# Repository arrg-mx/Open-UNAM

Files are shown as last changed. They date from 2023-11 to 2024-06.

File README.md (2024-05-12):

# Open-UNAM

## Contenido

- [Objetivo](#objetivo)
- [Desarrollo](#desarrollo)
- [Equipo](#equipo)
- [Referencias](#referencias)

## Objetivo

Diseñar he implementar una plataforma de pruebas basada en los parámetros del robot Open-Manipulator, la cual se realizán pruebas de algoritmos de manipulación de objetos.

## Desarrollo

- [X] Diseñar el modelo virtual de la platadorma del robot con 5 grados de libertad.
- [x] Cálcular el modelo cinemático inverso de las velocidades del robot para la realización de trayectorias.
- [ ] Implementar el modelo en Simulink del control del robot.
- [ ] Realizar pruebas de funcionamiento del sistema realizando una tarea simple.

Metas 2024-2
- [ ] Hacer una revisión de los componentes con los que se cuentan para la construcción del robot.
- [ ] Realizar la manufactura de las piezas del robot y realizar pruebas de ensamble.
- [ ] Rediseñar la base del robot para que el robot sea estable y garantice el correcto funcionamiento de su actuador.
- [ ] Trabajar en una interfaz de control de los motores en Matlab para que el robot realice una tarea específica. 

## Equipo

**Integrantes del proyecto:**

| Nombre | Observaciones | Semestre |
| :---| :--- | :--- |
| M.I. Erik Peña Medina | **Responsable** | ---- |
| Díaz Alcalá Leslie Zahori | **Participante** | 2024-1 |
| Chavez López Ana Rosa | **Participante** | 2024-1 |
| Rosas Torres Brian Ulises | **Participante** | 2024-1 |
| Pazarán García Jared | **Participante** | 2024-1 |
| Muñoz Ng Gustavo  | **Participante** | 2024-1 |
| Laureano Uribe Diego  | **Participante** | 2024-1 |
| Colima Flores Mauricio Gibran  | **Participante** | 2024-2 |
| Pascual Hernández Daniel Alfonso | **Participante** | 2024-2 |
| Vilchis Torres Itzel | **Participante** | 2024-2 |
| Rivera Moreno Javier | **Participante** | 2024-2 |

## Referencias

### ¿Dónde empezar?

**Academics**

1. Documentacion motor AX-18 [emanual] (https://emanual.robotis.com/docs/en/dxl/ax/ax-18a/)
2. Documentacion DYNAMIXEL Shield [emanual] (https://emanual.robotis.com/docs/en/parts/interface/dynamixel_shield/)
3. Documentacion OpenManipulator [emanual] (https://emanual.robotis.com/docs/en/platform/openmanipulator_x/overview/)
4. Repositorio ROS [github](https://github.com/ROBOTIS-GIT/open_manipulator/tree/master)
5. Archivos de referencia (Carpeta de CAD) [onshape] (http://www.robotis.com/service/download.php?no=690)

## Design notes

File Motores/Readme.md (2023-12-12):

# Conexión del motor AX-18A Dynamixel con Mathlab

## Conexión del programa con el Dynamixel Wizard:

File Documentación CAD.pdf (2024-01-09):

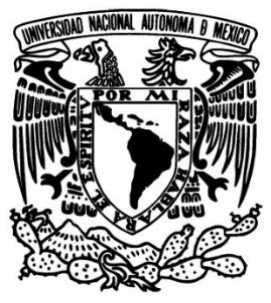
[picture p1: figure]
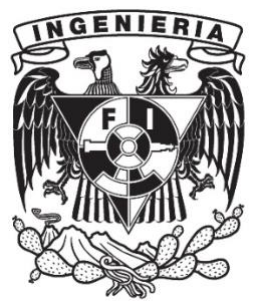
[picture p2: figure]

# Universidad Nacional Autónoma de México Facultad de Ingeniería División de Ingeniería Mecánica e Industrial

# Robótica

## Proyecto Open-Puma

# Documentación CAD

### Alumnos:

### Chávez López Ana Rosa

### Muñoz Ng Gustavo

### Grupo 01

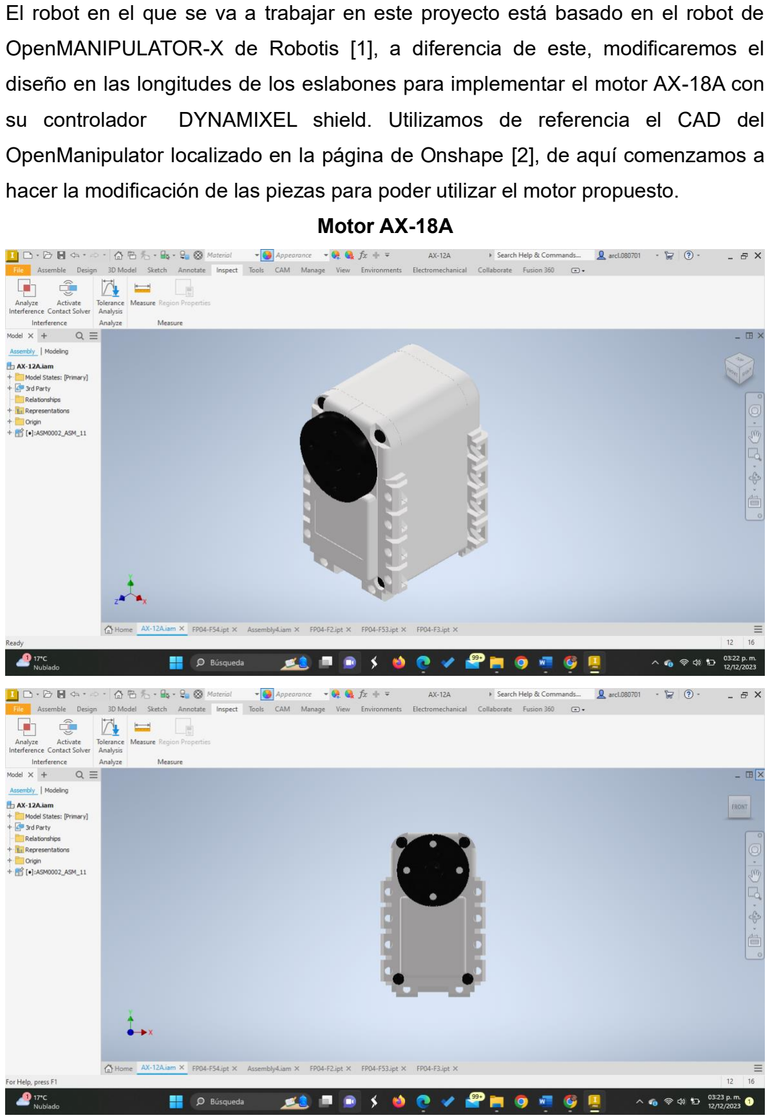
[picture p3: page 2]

El robot en el que se va a trabajar en este proyecto está basado en el robot de

OpenMANIPULATOR-X de Robotis [1], a diferencia de este, modificaremos el

diseño en las longitudes de los eslabones para implementar el motor AX-18A con

su controlador DYNAMIXEL shield. Utilizamos de referencia el CAD del

OpenManipulator localizado en la página de Onshape [2], de aquí comenzamos a

hacer la modificación de las piezas para poder utilizar el motor propuesto.

| Motor AX-18A

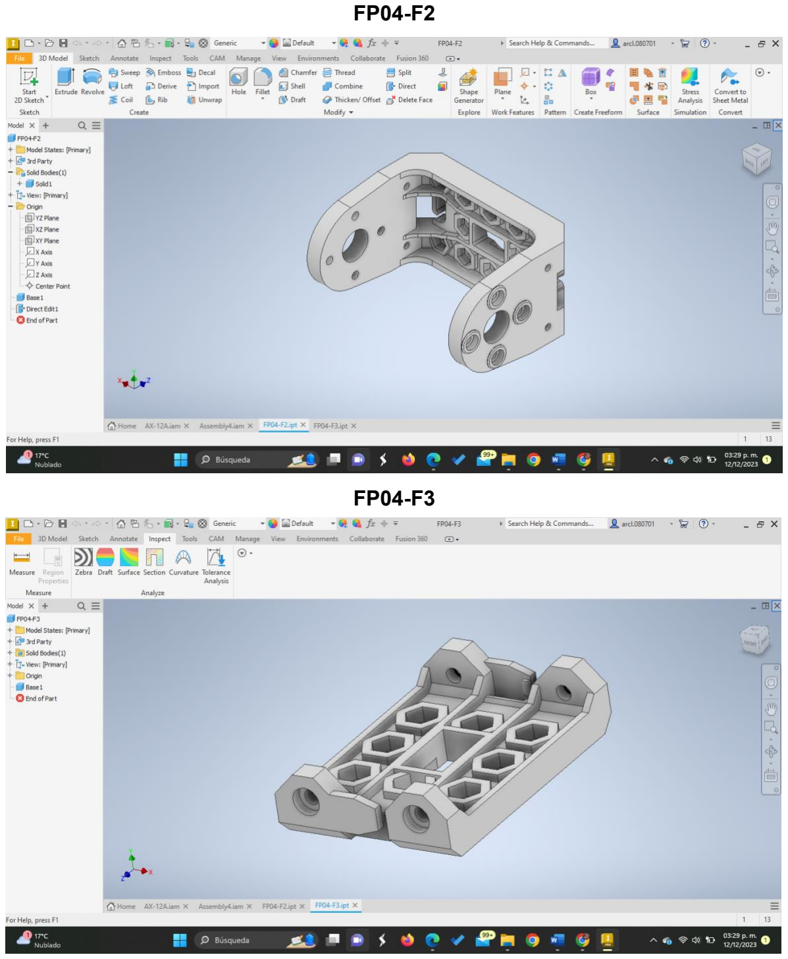
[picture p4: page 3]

FP04-F2

FP04-F3

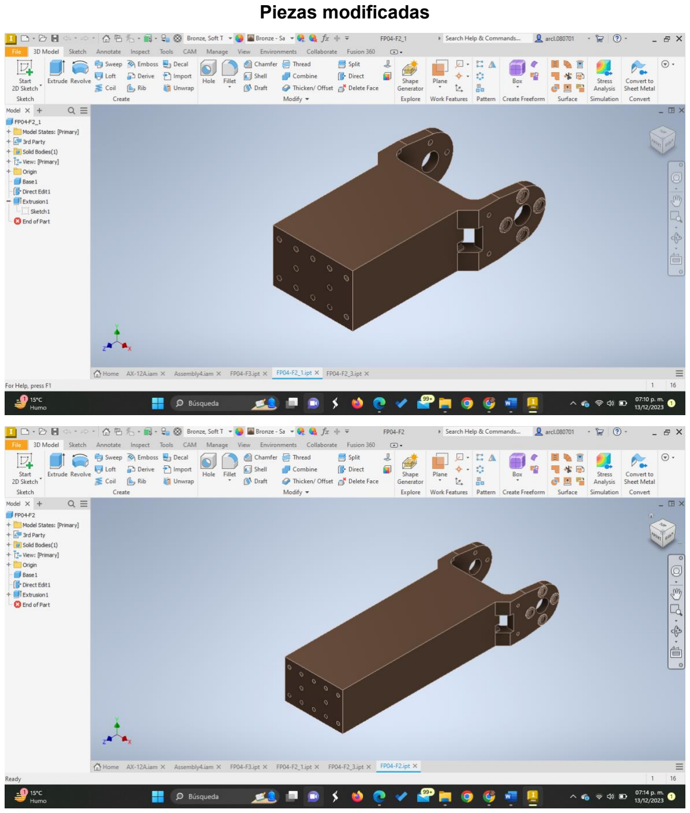
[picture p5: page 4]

Piezas modificadas

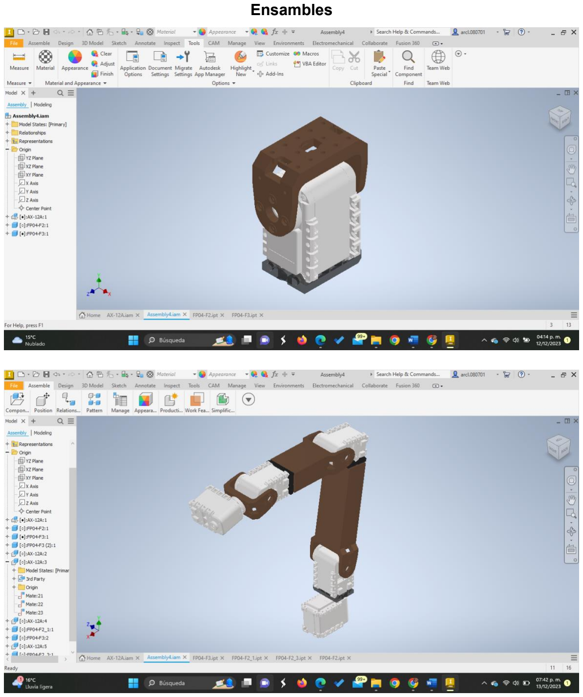
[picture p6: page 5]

Ensambles

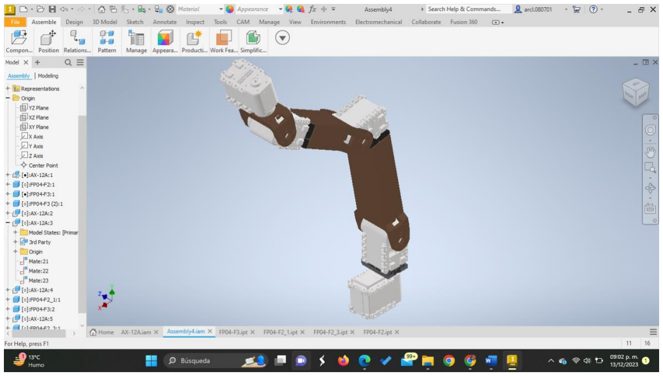
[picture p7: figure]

Referencias

[1] | «Robotis | e-manual,» | 2017. | [En | línea]. | Available:

https://emanual.robotis.com/docs/en/platform/openmanipulator_x/overview/.

[2] | «onshape,» | 2017. | [En | línea]. | Available:

https://cad.onshape.com/documents/9442f03bd8ccac084fda9dd3/w/039e8dbd53e078254

0ea5b0d/e/6f08aa8ac3d3e5b3054f7782. (https://cad.onshape.com/documents/9442f03bd8ccac084fda9dd3/w/039e8dbd53e0782540ea5b0d/e/6f08aa8ac3d3e5b3054f7782)

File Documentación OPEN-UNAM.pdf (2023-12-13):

### Universidad Nacional Autónoma De México

### Facultad de ingeniería

### División de Ingeniería Mecánica e Industrial

### Robótica

### Proyecto: OPEN-UNAM

Chávez López Ana Rosa

Díaz Alcalá Leslie Zahori

Laureano Uribe Diego

Muñoz Ng Gustavo

Pazarán García Jared

Rosas Torres Brian Ulises

### Semestre: 2024-1

El robot en el que se va a trabajar en este proyecto está basado en el robot de OpenMANIPULATOR-X [1], a diferencia de este, modificaremos el diseño en las longitudes de los eslabones para implementar el motor AX-18A con su controlador DYNAMIXEL shield.

Utilizamos de referencia el CAD del OpenManipulator localizado en la página de Onshape [2], de aquí comenzamos a hacer la modificación de los eslabones para poder utilizar el motor propuesto, las especificaciones del motor son las siguientes:

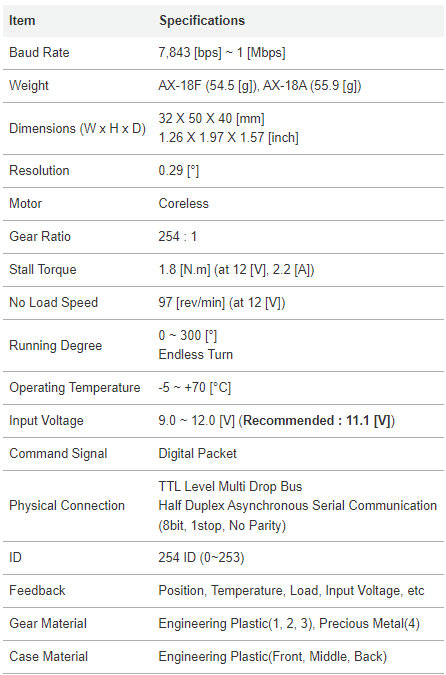
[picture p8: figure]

Este motor cuenta con un área EEPROM y un área RAM. Tabla de control del área EEPROM:

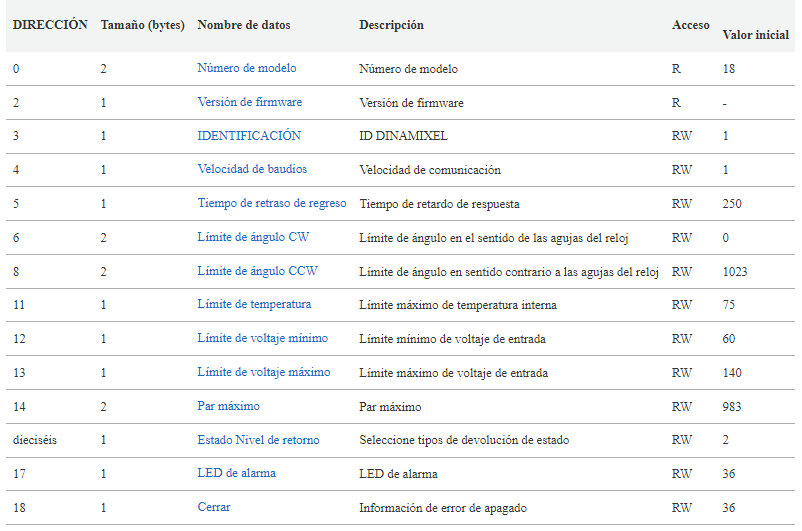
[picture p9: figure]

Área (EEPROM, RAM)
La Mesa de Control se divide en 2 Áreas. Los datos en el área RAM se restablecen a los valores iniciales cuando se restablece la alimentación (volátil). Por otro lado, los datos en el área EEPROM se mantienen incluso cuando el dispositivo está apagado (no volátil).

Tamaño
El tamaño de los datos varía de 1 a 2 bytes dependiendo de su uso. Verifique el tamaño de los datos cuando los actualice con un paquete de instrucciones. Los datos de más de 2 bytes se guardarán según Little Endian .

Acceso
La Mesa de Control tiene dos propiedades de acceso diferentes. La propiedad 'RW' significa permiso de acceso de lectura y escritura, mientras que 'R' significa permiso de acceso de solo lectura. Los datos con la propiedad de solo lectura no se pueden cambiar mediante la instrucción WRITE. La propiedad de solo lectura ('R') se usa generalmente para fines de medición y monitoreo, y la propiedad de lectura y escritura ('RW') se usa para controlar el dispositivo.

Valor inicial
Cada dato en la Tabla de control se restaura a los valores iniciales cuando se enciende el dispositivo. Los valores predeterminados en el área EEPROM son valores iniciales del dispositivo (configuraciones predeterminadas de fábrica). Si un usuario modifica algún valor en el área EEPROM, los valores modificados se restaurarán como valores iniciales cuando se encienda el dispositivo. Los valores iniciales en el área de RAM se restauran cuando se enciende el dispositivo.

Tabla de control del área RAM:

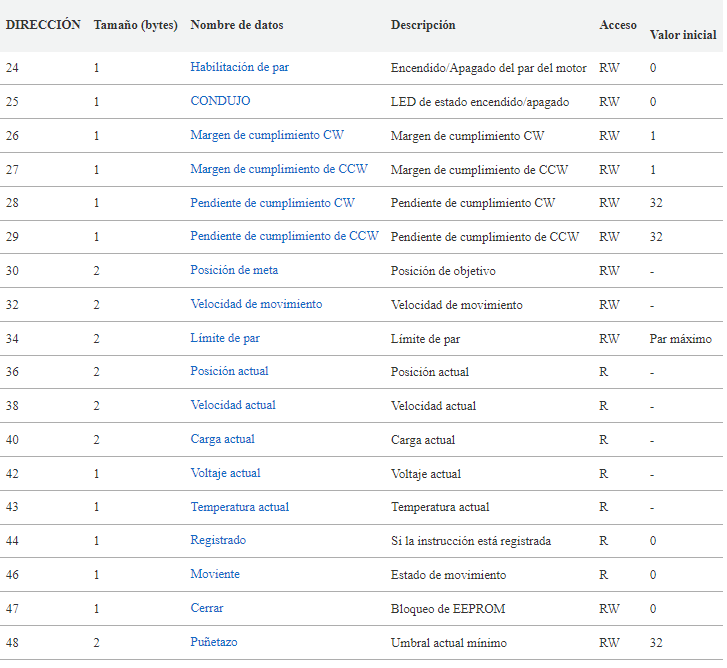
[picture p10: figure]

La velocidad en baudios determina la velocidad de comunicación en serie entre un controlador y DYNAMIXEL.

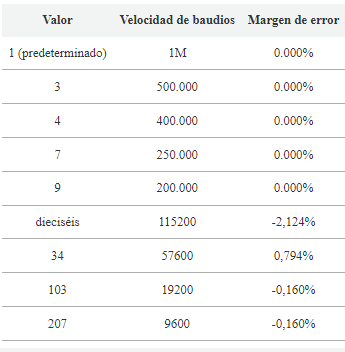
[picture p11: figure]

Ensamble del motor:

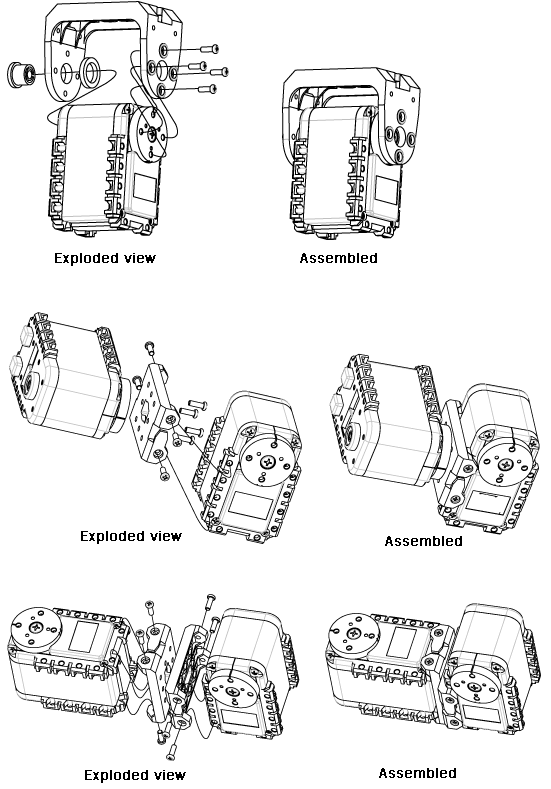
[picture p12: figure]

[3]

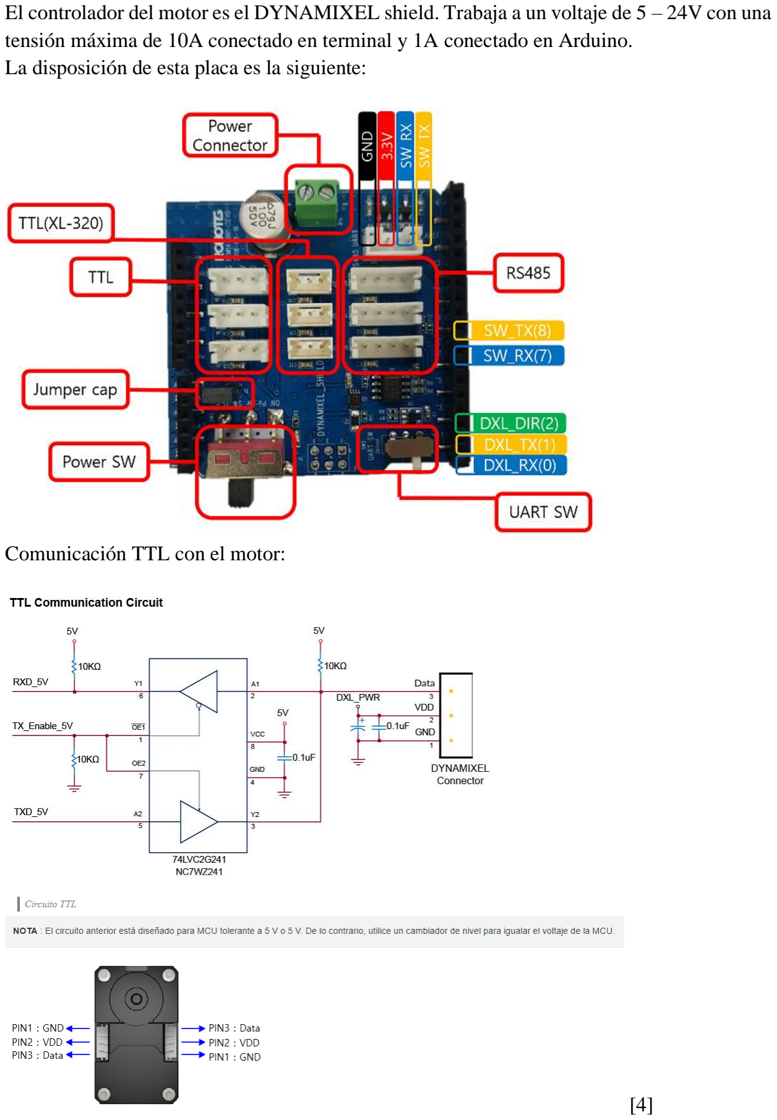
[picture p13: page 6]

El controlador del motor es el DYNAMIXEL shield. Trabaja a un voltaje de 5 – 24V con una tensión máxima de 10A conectado en terminal y 1A conectado en Arduino.
La disposición de esta placa es la siguiente:

Comunicación TTL con el motor:

[4]

El desarrollo de la dinámica del robot, así como el CAD de este, se encuentran en otros documentos dentro del repositorio de GitHub.

## Referencias

[
1
]

«Robotis e-manual,» 2017. [En línea]. Available: https://emanual.robotis.com/docs/en/platform/openmanipulator_x/overview/.

[
2
]

«onshape,» 2017. [En línea]. Available: https://cad.onshape.com/documents/9442f03bd8ccac084fda9dd3/w/039e8dbd53e0782540ea5b0d/e/6f08aa8ac3d3e5b3054f7782.
[
3
]

Dynamixel, «Robotis,» [En línea]. Available: https://emanual.robotis.com/docs/en/dxl/ax/ax-18a/.

[
4
]

Dynamixel, «Robotis,» [En línea]. Available: https://emanual.robotis.com/docs/en/parts/interface/dynamixel_shield/.

Software Utilizados:
Inventor
Matlab
Dynamixel WIZARD

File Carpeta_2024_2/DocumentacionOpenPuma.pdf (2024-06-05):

Open – Puma UNAM; UNIVERSIDAD NACIONAL; Robótica – Proyecto; Proyecto; Robótica; AUTÓNOMA DE MÉXICO; FACULTAD DE INGENIERÍA; Open-Puma UNAM; Profesor: Erick Peña Medina Semestre 2024 – 2 Grupo: 01; Alumnos: Colima Flores Mauricio Gibran Pascual Hernández Daniel Alfonso Rivera Moreno Javier Vilchis Torres Itzel

AUTÓNOMA DE MÉXICO | F A C U L T A D D E I N G E N I E R Í A DIVISIÓN DE INGENIERÍA MECÁNICA E INDUSTRIAL

Open – Puma UNAM | 2/40
AUTÓNOMA DE MÉXICO | F A C U L T A D D E I N G E N I E R Í A DIVISIÓN DE INGENIERÍA MECÁNICA E INDUSTRIAL Robótica – Proyecto

### Contenido

Open – Puma UNAM | 3/40
AUTÓNOMA DE MÉXICO | F A C U L T A D D E I N G E N I E R Í A DIVISIÓN DE INGENIERÍA MECÁNICA E INDUSTRIAL Robótica – Proyecto

## INTRODUCCIÓN

A lo largo del curso de Robótica se adquirieron herramientas que son de gran utilidad para analizar, diseñar y controlar un robot serial, desde los análisis de posición, hasta el cálculo de los modelos cinemáticos directo e inverso, todos estos indispensables para describir a nuestro objeto de estudio.
Sin embargo, bajo la premisa de que, como futuros profesionistas en el campo de la ingeniería, no sólo es necesario el conocimiento de un área, sino también la capacidad de implementarlo, es que un proyecto como Open-Puma se vuelve fundamental para nuestra formación ya que ofrece distintos retos y aprendizajes que amplían nuestra visión y complementan nuestro perfil académico.

Open-Puma es un proyecto en el que se busca diseñar, analizar, construir y evaluar un robot serial con 5 grados de libertad. Este robot en el que se trabajó está basado en el OpenMANIPULATOR-X [1], el cual fue modificado para la implementación del motor AX-18A con su controlador DYNAMIXEL shield.

Este proyecto fue trabajado previamente por alumnos del curso de robótica impartido en el semestre 2024-I, en donde se realizaron modificaciones de las piezas de ensamble, los análisis cinemáticos y dinámicos del robot, así como la documentación requerida para la implementación del controlador DYNAMIXEL shield.

En el caso de este equipo, se seguirá trabajando con las etapas de la manufactura, ensamble, control y evaluación del proyecto propuesto anteriormente, no sin antes realizar una evaluación general de la condición actual del proyecto para realizar ajustes o modificaciones en caso de ser necesarias con respecto al trabajo realizado el curso anterior.

Open – Puma UNAM | 4/40
AUTÓNOMA DE MÉXICO | F A C U L T A D D E I N G E N I E R Í A DIVISIÓN DE INGENIERÍA MECÁNICA E INDUSTRIAL Robótica – Proyecto

## OBJETIVO

- Hacer una revisión de los componentes con los que se cuentan para la construcción del robot.
- Realizar la manufactura de las piezas del robot y realizar pruebas de ensamble.
- Rediseñar la base del robot para que el robot sea estable y garantice el correcto funcionamiento de su actuador.
- Trabajar en una interfaz de control de los motores en Matlab para que el robot realice una tarea específica.

## RUBRICA

La evaluación del siguiente proyecto será definida por el profesor con respecto a los avances entregados en este reporte y documentos agregados al apartado de GitHub.

## EVALUACIÓN

Se deben desarrollar los siguientes puntos:
1. Lista de partes.
2. Base del robot.
3. Control del robot.
4. Manufactura y ensamble de las piezas.

## DESARROLLO

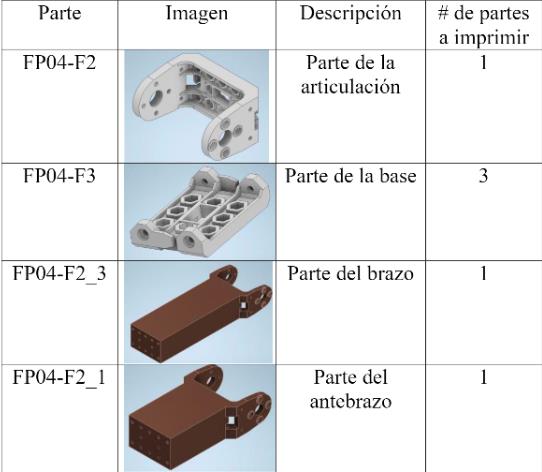
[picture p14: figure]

Open – Puma UNAM | 5/40
AUTÓNOMA DE MÉXICO | F A C U L T A D D E I N G E N I E R Í A DIVISIÓN DE INGENIERÍA MECÁNICA E INDUSTRIAL Robótica – Proyecto

LISTA DE PARTES

Para el desarrollo de esta parte se contempló realizar una lista de partes, la cual nos diera una guía de todos los elementos que se mandarían a imprimir. En primera instancia, se pensaba partir del trabajo realizado anteriormente y considerar las partes creadas por el equipo que trabajó en este proyecto durante el semestre 2024-I. De tal manera que, nuestra primera lista de componentes se constituyó de la siguiente manera:

Tabla 1 Lista de partes versión 1
A primera vista el ensamble del robot parecía tener todo en orden, sin embargo, la brigada tuvo la observación por parte del profesor de la falta de métodos de unión entre las piezas y los servomotores, por lo que se tuvo que realizar un análisis tanto de los eslabones como del ensamble para ver si estas eran adecuadas para su implementación o era necesario realizar ajustes o rediseños en todos los componentes propuestos.

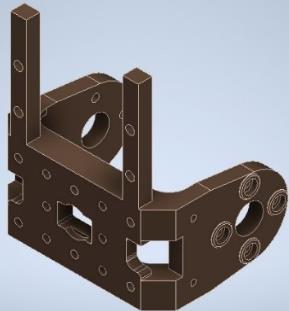
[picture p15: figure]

Open – Puma UNAM | 6/40
AUTÓNOMA DE MÉXICO | F A C U L T A D D E I N G E N I E R Í A DIVISIÓN DE INGENIERÍA MECÁNICA E INDUSTRIAL Robótica – Proyecto

Figura 1. Vista del ensamble primera versión
Después del análisis del ensamble de esta primera lista de componentes generados en el semestre anterior 2024-I, se propuso una nueva lista de componentes, realizando modificaciones a las piezas tanto en su geometría, como añadiendo elementos que permitieran unir el eslabón con el servomotor. Es así que la segunda versión de lista de componentes contó con estas modificaciones además de un caso en particular en donde se optó por sustituir la pieza “FP04-F2_3” por una segunda pieza “FP04-F2_1”, además se eliminó la pieza “FP04-F3” y crear otra que cumpliera con su misma función a partir de modificaciones de “FP04-F2”.
Figura 2. Modificación 1 FP04-F2 | Figura 3. Modificación 2 FP04-F2

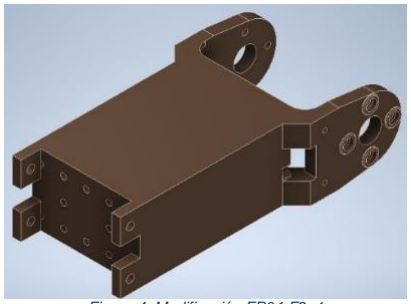
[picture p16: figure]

Open – Puma UNAM | 7/40
AUTÓNOMA DE MÉXICO | F A C U L T A D D E I N G E N I E R Í A DIVISIÓN DE INGENIERÍA MECÁNICA E INDUSTRIAL Robótica – Proyecto

Figura 4. Modificación FP04-F2_1
Con estas modificaciones se realizó la segunda versión de la lista de componentes, en esta se un método de unión roscada, esta lista también presentó errores debido a parámetros que no fueron tomados en cuenta tales como las dimensiones del servomotor o la distancia entre los barrenos de sus guías, por lo que se procedió a realizar nuevamente modificaciones a las piezas.

Tabla 2 Lista de componentes versión 2

Open – Puma UNAM | 8/40
AUTÓNOMA DE MÉXICO | F A C U L T A D D E I N G E N I E R Í A DIVISIÓN DE INGENIERÍA MECÁNICA E INDUSTRIAL Robótica – Proyecto

En esta iteración, se renombraron las piezas para poder ubicarlas de mejor manera. Las correcciones que se tuvieron que hacer fueron sobre las piezas “FP04-F2_3” este rediseño se puede apreciar a continuación.

Figura 5. Modificación FP04-F2_3
La tercera versión de la lista de componentes quedó de la siguiente manera, sin embargo nuevamente se tuvieron que hacer ajustes en las piezas “FP04-F2_3” y “FP04-F2_2”

Tabla 3. Lista de componentes versión 3

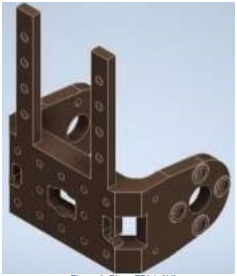
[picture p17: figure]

Open – Puma UNAM | 9/40
AUTÓNOMA DE MÉXICO | F A C U L T A D D E I N G E N I E R Í A DIVISIÓN DE INGENIERÍA MECÁNICA E INDUSTRIAL Robótica – Proyecto

Se realizaron modificaciones a las piezas mencionadas anteriormente y también se volvieron a renombrar las piezas, esto con el objetivo no sólo de identificarlas sino también con la intención de evidenciar las iteraciones de diseño que se tuvieron que aplicar a cada pieza que fungirá como eslabón dentro del robot. Es así que las piezas “FP04-F2_1”, “FP04-F2_2” y “FP04-F2_3” serán renombradas como “FP04_2V1”, “FP04_3V2” y “FP04_1V3” respectivamente, en donde la terminación “Vx” significa versión seguida por el número que corresponde a las iteraciones que se implementaron en el rediseño de la pieza.

Figura 6. Pieza FP04_3V2 | Figura 7. Pieza FP04_1V3
Antes de dar por finalizada esta etapa es necesario realizar una prueba de colisiones en el ensamble para poder estar seguros de que estas piezas pueden cumplir con su función y no darán problemas a la hora de la construcción del robot, para esto nos apoyamos del software Fusion 360. Una vez que revisamos que no hay colisiones podemos pasar a la siguiente etapa del proyecto.

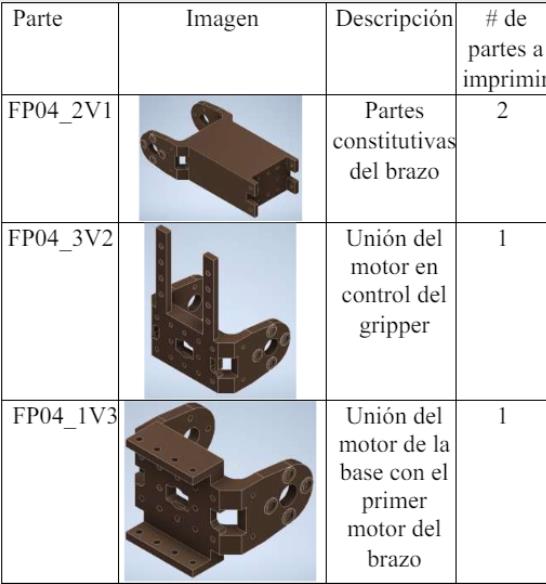
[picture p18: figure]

Open – Puma UNAM | 10/40
AUTÓNOMA DE MÉXICO | F A C U L T A D D E I N G E N I E R Í A DIVISIÓN DE INGENIERÍA MECÁNICA E INDUSTRIAL Robótica – Proyecto

Figura 8. Prueba de colisiones del ensamble
Después de revisar que no existieran colisiones en nuestro ensamble podemos pasar a la siguiente etapa del proyecto, la versión final de la lista de componentes se muestra a continuación.

Tabla 4. Lista de componentes versión 4

Open – Puma UNAM | 11/40
AUTÓNOMA DE MÉXICO | F A C U L T A D D E I N G E N I E R Í A DIVISIÓN DE INGENIERÍA MECÁNICA E INDUSTRIAL Robótica – Proyecto

BASE DEL ROBOT

Dado que no se contaba con un diseño previo de la base se realizó la valoración de diversas opciones y así saber la opción más viable para continuar con el análisis del proyecto, para lo mismo se plantearon 3 opciones: Comprar la base, rediseñar la base, obtener un modelo CAD libre de un tercero. Tras el análisis de las 3 opciones los resultados fueron los siguientes:

- Comprar a base:
Se consultó con dos tiendas diferentes; Sandorobotics [2] y Génération Robots [3], sin embargo, el producto estaba fuera de stock en una de ellas y en la otra el precio era demasiado elevado, por lo que la opción de comprar la base quedó descartada.

Figura 9. Base Sandorobotics agotada

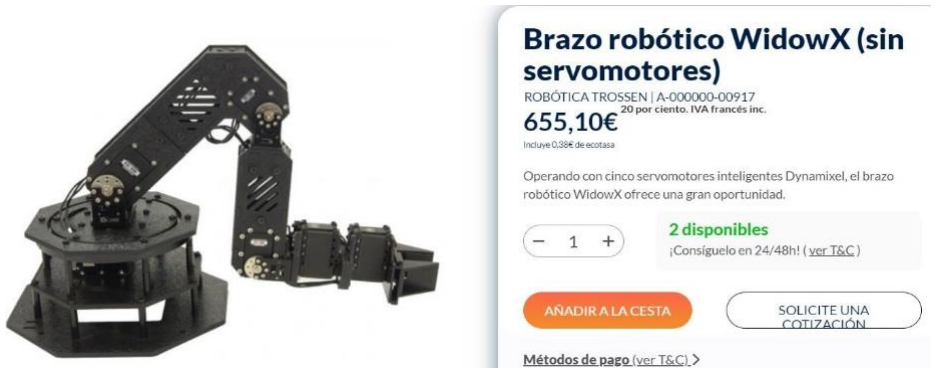
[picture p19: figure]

Open – Puma UNAM | 12/40
AUTÓNOMA DE MÉXICO | F A C U L T A D D E I N G E N I E R Í A DIVISIÓN DE INGENIERÍA MECÁNICA E INDUSTRIAL Robótica – Proyecto

Figura 10. Base Génération Robots presupuesto

- Rediseñar la base:
Teniendo el modelo físico que se encuentra en el laboratorio, se pueden sacar medidas para obtener un modelo en CAD y realizar un prototipo rápido con el que se puedan realizar pruebas y hacer ajustes si es necesario en cuanto a medidas o a materiales.
- Modelo CAD obtenido por terceros:
Se encontraron diversos modelos ya diseñados, algunos de ellos de uso libre y otro más con costo (Todos los modelos se encuentran en el documento “Revisión para base de robot open-puma” [4]), sin embargo se decidió utilizar una propuesta del modelo InterbotiX PhantomX, obtenida directamente de la página de GRABCAD COMMUNITY [5]. Esta propuesta fue la elegida por la facilidad de manufacturar la base por placas a través de la corte láser e impresión 3D.

Open – Puma UNAM | 13/40
AUTÓNOMA DE MÉXICO | F A C U L T A D D E I N G E N I E R Í A DIVISIÓN DE INGENIERÍA MECÁNICA E INDUSTRIAL Robótica – Proyecto

Figura 11. Modelo robot InterbotiX PhantomX

Posteriormente de elegir el CAD se tomó el archivo del ensamble completo “bases_juntas”, ara poder obtener las distintas placas que componen la base del robot se tuvo que duplicar ese archivo e ir eliminando todos los componentes excepto la placa requerida para poder tener una sola pieza y poder trabajar de forma adecuada cada una. Este proceso se realizó para cada una de las piezas de la placa.

Figura 12. Lista de componentes de la base

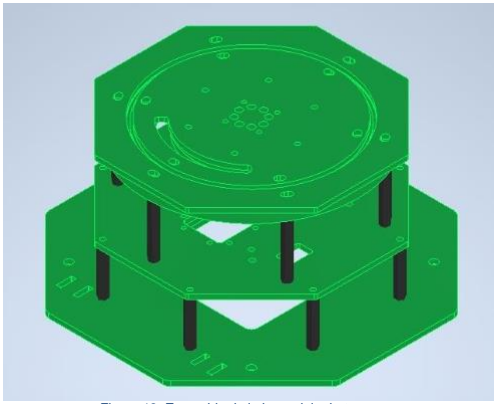
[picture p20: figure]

Open – Puma UNAM | 14/40
AUTÓNOMA DE MÉXICO | F A C U L T A D D E I N G E N I E R Í A DIVISIÓN DE INGENIERÍA MECÁNICA E INDUSTRIAL Robótica – Proyecto

Posteriormente se realizó un análisis del ensamble, con el cual se logró determinar que las piezas serian fabricadas por medio de corte láser dado que poseen el mismo grosor de 3 [mm], siendo más fácil y rápido que imprimirlas. Las piezas que se cortan son las siguientes:
- Base_enmedio.ipt
- Base_inferior.ipt
- Base_sup.ipt
- Base_sup_mov.ipt
- Base_sup_mov_2.ipt
- Tapa_base_sup.ipt

Figura 13. Ensamble de la base del robot
Para poder comenzar el proceso de corte, primero se plasmó en inventor las proyecciones de las placas y se exportaron como archivos con extensión “.dwg” en la versión 2013, este archivo generado se debe de pasar a Fusión 360 creando un nuevo proyecto y cargando el archivo para proyectar las formas en el “dibujo”, es necesario quitar el margen y cajetín para finalmente convertirlo a un archivo tipo “.dxf” que podrá ser ingresado al software de la cortadora.

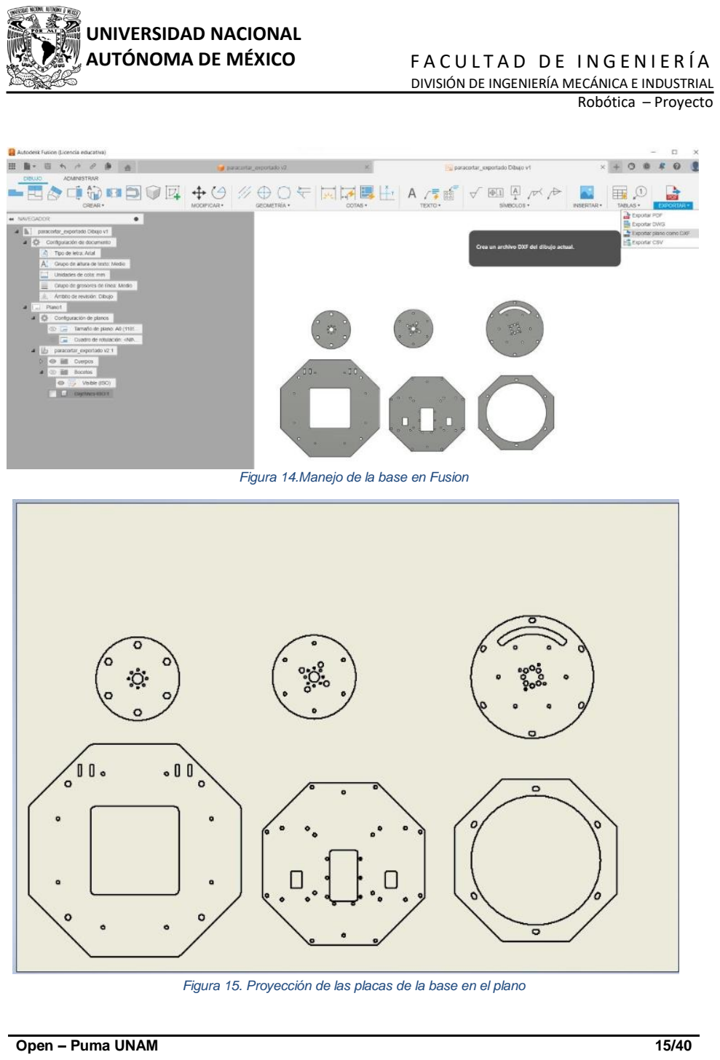
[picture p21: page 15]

Open – Puma UNAM | 15/40
AUTÓNOMA DE MÉXICO | F A C U L T A D D E I N G E N I E R Í A DIVISIÓN DE INGENIERÍA MECÁNICA E INDUSTRIAL Robótica – Proyecto

Figura 14.Manejo de la base en Fusion

Figura 15. Proyección de las placas de la base en el plano

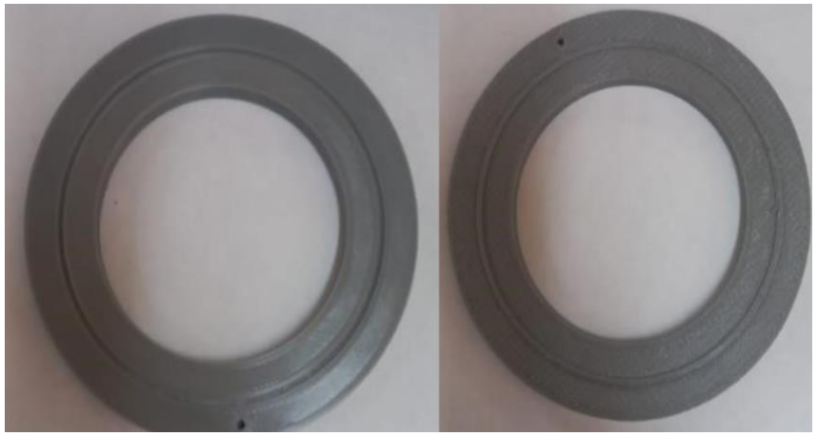
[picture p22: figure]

Open – Puma UNAM | 16/40
AUTÓNOMA DE MÉXICO | F A C U L T A D D E I N G E N I E R Í A DIVISIÓN DE INGENIERÍA MECÁNICA E INDUSTRIAL Robótica – Proyecto

Durante la exportación del documento a la computadora de la cortadora, se debe verificar el mandar el archivo a la máquina, dado que el software utilizado no puede leer en primera instancia los archivos “.dxf” es necesario agregarlos desde el apartado de exportación. Una vez el archivo fue cargado se puede comenzar con el corte.
Una pieza de la base se fabricó por medio de manufactura aditiva (3d_1.ipt) para luego solo determinar el valor de los balines adecuados para su construcción. El manejo de las piezas a manufacturar por medio de impresión 3D se muestran en el apartado de manufactura y ensamble.

Figura 16. Pieza de la base impresa en 3D

Se le retiraron los soportes y dimensionalmente cumple con lo establecido. Para este caso los separadores entre las distintas placas son de 3[mm] de diámetro y los balines de la parte superior de la base son de 8[mm] de diámetro.

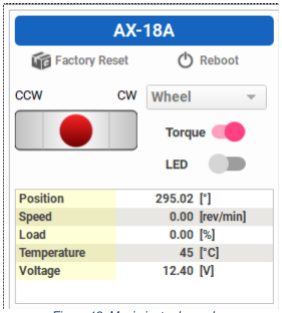
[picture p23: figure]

Open – Puma UNAM | 17/40
AUTÓNOMA DE MÉXICO | F A C U L T A D D E I N G E N I E R Í A DIVISIÓN DE INGENIERÍA MECÁNICA E INDUSTRIAL Robótica – Proyecto

CONTROL DEL ROBOT

Para el control del robot tomaremos como apoyo el uso de motores, que en este caso serán los AX-18A, y los AX-12A. Estos servomotores cuentan con; una gran precisión, durabilidad y una alta facilidad de control, dichas características serán de gran beneficio para el desarrollo de nuestro robot. Recordemos que este robot trabaja a 12 [V], y cuenta con un par de torsión de 1.8 [Nm], una velocidad de hasta 97 rpm . Su rango de movimiento va desde los 0° hasta los 300° {Ref}, sin embargo, también puede operar de manera continua. [6]

Tipos de movimiento
A continuación, tenemos un par de ejemplos de las maneras mediante las cuales se puede operar el servomotor.
Figura 17. Movimiento controlado | Figura 18. Movimiento de rueda
En el caso de movimiento controlado, podemos elegir la posición exacta en la que queremos que se mueva el servomotor, mientras que, para el movimiento de rueda, el servomotor semeja su comportamiento más al de una llanta en movimiento.

Open – Puma UNAM | 18/40
AUTÓNOMA DE MÉXICO | F A C U L T A D D E I N G E N I E R Í A DIVISIÓN DE INGENIERÍA MECÁNICA E INDUSTRIAL Robótica – Proyecto

Driver de los servomotores

Para controlar los servomotores tomamos como apoyo DINAMIXEL shield y Wizard 2.0.

Figura 19. Placa controladora
Conectamos el servomotor al driver, a su vez esta placa est.aba conectada a alimentación y a la laptop. Tal y como se puede apreciar en la siguiente ilustración:

Figura 20. Conexión del servo

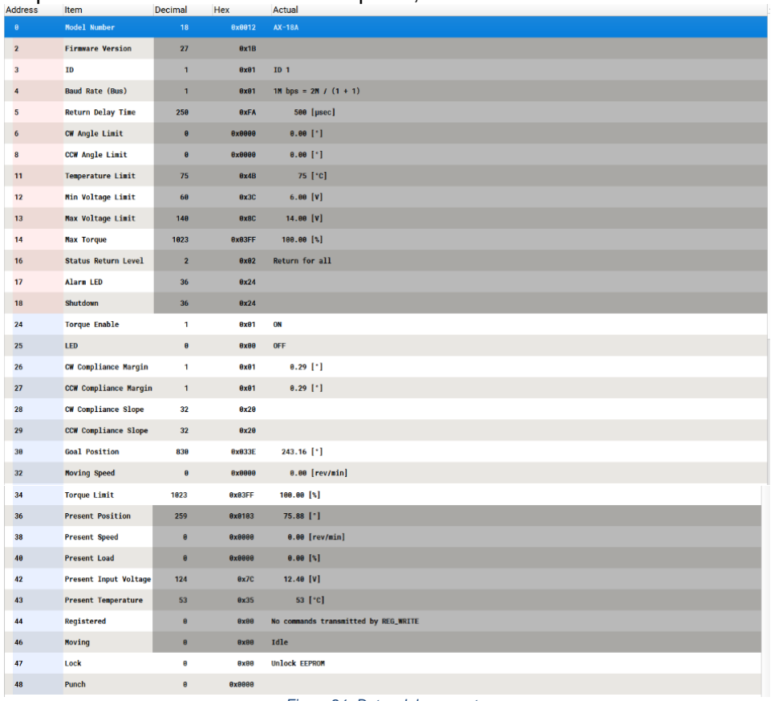
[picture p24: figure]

Open – Puma UNAM | 19/40
AUTÓNOMA DE MÉXICO | F A C U L T A D D E I N G E N I E R Í A DIVISIÓN DE INGENIERÍA MECÁNICA E INDUSTRIAL Robótica – Proyecto

Una vez que el servomotor estaba conectado a la placa y a la laptop, haciendo uso de la herramienta Wizard 2.0, obtuvimos los datos necesarios. Para emplear esta herramienta era necesario buscar y seleccionar el puerto al que se encontraba conectada la placa, en nuestro caso COM5.

Figura 21. Datos del sevomotor
Conexión de los servomotores

De manera unitaria
Para conectar un solo servomotor era necesario seguir el diagrama de la Ilustración 17, y de esta manera obteníamos la siguiente conexión:


Open – Puma UNAM | 20/40
AUTÓNOMA DE MÉXICO | F A C U L T A D D E I N G E N I E R Í A DIVISIÓN DE INGENIERÍA MECÁNICA E INDUSTRIAL Robótica – Proyecto

Figura 22. Conexión unitaria

En serie
Para poder conectar todos los servomotores que se necesitarían para el proyecto y obtener sus respectivas tablas de datos en Wizard 2.0. Fue necesario conectarlos en serie, un contratiempo contra tiempo con el cual nos enfrentamos es que los servos tienen que conectarse de una manera específica. La primera entrada va conectada a la segunda del siguiente servomotor y al finalizar con la conexión en serie, del ultimo servomotor cometamos la primera entrada a la placa.

Figura 23. Conexión en serie


Open – Puma UNAM | 21/40
AUTÓNOMA DE MÉXICO | F A C U L T A D D E I N G E N I E R Í A DIVISIÓN DE INGENIERÍA MECÁNICA E INDUSTRIAL Robótica – Proyecto

De esta manera nuestro Wizard 2.0, va a registrar de un solo puerto todos los servomotores que se encuentren conectados en serie.

Figura 24. Registro de los 4 servomotores
Desarrollo del código

Para el desarrollo de este código tomamos como base el que se encontraba en la carpeta del GitHub, con el nombre de “DynamixelSDK-3.7.3”. Este código se trabajó en MATLAB.
Para poder acceder a archivo, dentro de la carpeta DynamixelSDK-3.7.31, teníamos una subcarpeta llamada “Matlab”, de la cual seleccionamos el protocolo 2.0. Una vez dentro abrimos el archivo “read_write”.

Open – Puma UNAM | 22/40
AUTÓNOMA DE MÉXICO | F A C U L T A D D E I N G E N I E R Í A DIVISIÓN DE INGENIERÍA MECÁNICA E INDUSTRIAL Robótica – Proyecto

Figura 25. Parte del código "read_write" sin editar

Comprensión del código
Para poder comprender este código fue necesario tomar como apoyo una playlist de tutoriales. Los cuales se pueden encontrar en el siguiente enlace:

https://youtube.com/playlist?list=PLEf1s0tzVSnQatNEj_TMwnv86f0IuvVa9&si=d5fGBUv68ZcJ-ezf (https://youtube.com/playlist?list=PLEf1s0tzVSnQatNEj_TMwnv86f0IuvVa9&si=d5fGBUv68ZcJ-ezf)

Dentro de esta playlist, nos encontramos con el video número 12, el cual nos lleva de la mano paso a paso para entender el código y cambiar el puerto, que en este caso fue de COM1 a COM5. Sin embargo, esto no era todo lo que se le debía modificar al código, ya que los valores y datos asignados que podemos ver en la ilustración 25, debían ser modificados por los del servomotor conectado, ilustración 21.

Este código nos permitía inicializar y comunicarnos con los servomotores.

Al ser un código considerablemente grande me tomé la libertad de comentar cada una de sus líneas de código explicando a detalle que hace cada parte, tal como se puede mostrar a continuación.


Open – Puma UNAM | 23/40
AUTÓNOMA DE MÉXICO | F A C U L T A D D E I N G E N I E R Í A DIVISIÓN DE INGENIERÍA MECÁNICA E INDUSTRIAL Robótica – Proyecto

Figura 26. Código explicado


Open – Puma UNAM | 24/40
AUTÓNOMA DE MÉXICO | F A C U L T A D D E I N G E N I E R Í A DIVISIÓN DE INGENIERÍA MECÁNICA E INDUSTRIAL Robótica – Proyecto

Primera iteración
Como se mencionó anteriormente, no bastaba con cambiar solo el puerto, sino que también fue necesario cambiar todos los datos y valores correspondientes:

Figura 27. Primera iteración
Fue en esta parte en donde se presentaron más problemas. El primero de nuestros problemas fue que para poder ejecutar el código en MATLAB era necesario desconectar el servomotor del Wizard 2.0. El segundo problema se presentó porque al ejecutar una vez el archivo en MATLAB, este no se podía ejecutar directamente por segunda vez, sino que requería reiniciar el entorno de programación. Debido a estos detalles era muy tardado poder realizar las pruebas correspondientes y calibrar los servomotores.

Es necesario mencionar que estos problemas no fueron los únicos que se presentaron, ya que el código, no permitía cambiar posición en la que se encontraba el servomotor, sino que tomaba directamente la posición que se encontraba escrita en las variables DXL_MINIMUM_POSITION_VALUE y en DXL_MAXIMUM_POSITION_VALUE.

Además, no movía el servomotor.

Open – Puma UNAM | 25/40
AUTÓNOMA DE MÉXICO | F A C U L T A D D E I N G E N I E R Í A DIVISIÓN DE INGENIERÍA MECÁNICA E INDUSTRIAL Robótica – Proyecto

Segunda iteración
Para la segunda iteración se agregó una interacción con el usuario en la interfaz, esto para poder solicitar una posición especifica que entrara dentro del rango de movimiento de nuestro servomotor, el cual se encontraba entre 2 y 1023:

Ilustración 28. Rango de movimiento

Figura 29. Cambios para segunda iteración
Además, para este código se agregaron líneas que permitieran interactuar directamente con el usuario y darle la información del rango en el que se puede mover el servo:


Open – Puma UNAM | 26/40
AUTÓNOMA DE MÉXICO | F A C U L T A D D E I N G E N I E R Í A DIVISIÓN DE INGENIERÍA MECÁNICA E INDUSTRIAL Robótica – Proyecto

Open – Puma UNAM | 27/40
AUTÓNOMA DE MÉXICO | F A C U L T A D D E I N G E N I E R Í A DIVISIÓN DE INGENIERÍA MECÁNICA E INDUSTRIAL Robótica – Proyecto

Figura 30. Codigo de la segunda iteración
Pese a que se comprobó la funcionalidad del código, seguía sin poder mover el servomotor. Conectaba el código con la posición del servomotor, sin embargo, no cambiaba a este de posición.

Para intentar solucionarlo se probó con varios rangos, ya que nuestra teoría suponía que la conexión no era posible porque el rango no era correcto. Pero aun cambiando el rango, el servomotor seguía sin moverse.

Tercera iteración
En la tercera iteración volví a modificar el código para que este pudiera comunicarse con 2 servomotores al mismo tiempo. Con el propósito de no tener que volver a hacer todo el código otra vez y adaptarlo a la última versión de servomotores se optó por trabajar con la misma versión de servos (AX-18A).

Open – Puma UNAM | 28/40
AUTÓNOMA DE MÉXICO | F A C U L T A D D E I N G E N I E R Í A DIVISIÓN DE INGENIERÍA MECÁNICA E INDUSTRIAL Robótica – Proyecto


Open – Puma UNAM | 29/40
AUTÓNOMA DE MÉXICO | F A C U L T A D D E I N G E N I E R Í A DIVISIÓN DE INGENIERÍA MECÁNICA E INDUSTRIAL Robótica – Proyecto

Figura 31. Código de la tercera iteración

Aunque se intentó de muchas maneras que la interfaz de MATLAB lograra mover los servomotores esto no fue posible. Además, la plataforma complicó mucho las pruebas, ya que para cada intento se tenía que reiniciar todo, de lo contrario no se ejecutaba el código.

Por las iteraciones realizadas puedo sugerir que es mejor cambiar la plataforma MATLAB, por una que sea mucho más fácil de usar; como lo es Arduino o en su defecto ROS que, aunque requiera de buenos conocimiento en Linux puede llegar a ser mucho más rápido que MATLAB.

Restricción del movimiento de los servomotores

Para el movimiento de Open-Puma, fue necesario establecer un rango de posiciones entre cada servomotor que articulaba la pieza. Esto es fundamental debido a que sin estas restricciones los componentes pueden llegar a chocar entre sí o a forzar demasiado la pinza y romperla.

Por ello desde Wizard 2.0, asignamos las restricciones a cada uno de los servomotores, de acuerdo a los movimientos que debía hacer cada uno de ellos:

Restricción del segundo motor a la base:
Cuenta con una posición máxima de 211 y una posición mínima de 638:

Open – Puma UNAM | 30/40
AUTÓNOMA DE MÉXICO | F A C U L T A D D E I N G E N I E R Í A DIVISIÓN DE INGENIERÍA MECÁNICA E INDUSTRIAL Robótica – Proyecto

Figura 32.Restricción del segundo motor a la base

Restricción del tercer motor a la base:
Cuenta con una posición máxima de 338 y una posición mínima de 846:

Figura 33.Restricción del tercer motor a la base


Open – Puma UNAM | 31/40
AUTÓNOMA DE MÉXICO | F A C U L T A D D E I N G E N I E R Í A DIVISIÓN DE INGENIERÍA MECÁNICA E INDUSTRIAL Robótica – Proyecto

Restricción del cuarto motor a la base:
Cuenta con una posición máxima de 209 y una posición mínima de 638:

Figura 34.Restricción del cuarto motor a la base

Restricción del motor que controla la pinza:
Cuenta con una posición máxima de 561 y una posición mínima de762:

Figura 35. Restricción del motor que controla la pinza


Open – Puma UNAM | 32/40
AUTÓNOMA DE MÉXICO | F A C U L T A D D E I N G E N I E R Í A

DIVISIÓN DE INGENIERÍA MECÁNICA E INDUSTRIAL Robótica – Proyecto

Video de las restricciones de los servos:
En el siguiente enlace se podrá encontrar el movimiento de los servomotores con sus respectivas restricciones:

https://www.youtube.com/watch?v=Bx20I3kAxpY

MANUFACTURA Y ENSAMBLE DE LAS PIEZAS

Para la fabricación de las piezas se optó por el método de manufactura aditiva, es decir por medio de impresión 3D. A lo largo de las distintas pruebas se utilizaron dos impresoras de la marca CREALITY; una Ender-3 V2 con un filamento de PLA y una Ender-3 V2 Neo con un filamento de PETG.
A lo largo de esta etapa hubo diversas iteraciones debido a diferentes causas, entre ellas, la nula experiencia por parte del equipo con este método de manufactura, los errores de diseño que hubo en las distintas piezas y las fallas recurrentes por parte de la impresora Ender-3 V2. Todas estas iteraciones se ven reflejadas en el documento de “Pruebas de manufactura aditiva” [7].
Figura 36.Ender-3 V2 Neo | Figura 37.Ender-3 V2


Open – Puma UNAM | 33/40
AUTÓNOMA DE MÉXICO | F A C U L T A D D E I N G E N I E R Í A DIVISIÓN DE INGENIERÍA MECÁNICA E INDUSTRIAL Robótica – Proyecto

Como primer paso, es necesario generar los archivos que la máquina pueda leer para realizar la impresión a partir de los modelos de las piezas realizados en CAD. Dado que la impresora tiene distintos parámetros a tomar en cuenta como el material de impresión, los soportes de la pieza, la densidad de relleno o el diámetro de la boquilla del extrusor, es necesario utilizar un software que nos permita configurar todos estos parámetros, ya que nuestro CAD no tiene estas herramientas.
El programa que vamos a utilizar es UltiMaker Cura (Versión 5.7.1), un software de uso libre en donde podemos realizar toda la configuración necesaria de las piezas y generar un archivo que la impresora pueda leer para realizar su trabajo. Cabe mencionar que con este programa es posible exportar dos piezas en la misma área de trabajo para que se puedan imprimir ambas al mismo tiempo sin necesidad de generar dos archivos diferentes.

Figura 38.Pantalla de carga UltiMaker Cura

Para poder empezar a trabajar con este programa debemos de generar los archivos de las piezas con extensión “.stl”, estos pueden ser generados con el CAD “Autodesk Fusion” a partir del modelo con extensión “.ipt” de la pieza. Una vez que se tiene la pieza en archivo “.stl” se puede importar desde la interfaz de UltiMaker Cura para agregarla al espacio de trabajo, este software nos permite importar varias piezas en el mismo espacio de trabajo e imprimir más de una al mismo tiempo.

Open – Puma UNAM | 34/40
AUTÓNOMA DE MÉXICO | F A C U L T A D D E I N G E N I E R Í A DIVISIÓN DE INGENIERÍA MECÁNICA E INDUSTRIAL Robótica – Proyecto

Dentro de la interfaz podemos posicionar y orientar cada elemento de manera que nos resulte más conveniente, la postura de las piezas es de gran importancia a la hora de la manufactura, ya que los tiempos de impresión, la calidad del acabado superficial y la cantidad de material utilizado pueden variar. También se deben de considerar los soportes auxiliares que se impriman junto con la pieza, ya que igualmente la cantidad de soportes, y por tanto de material utilizado, pueden ser mayores o menores.
Una vez que tenemos nuestros modelos con la postura adecuada, debemos de modificar los distintos parámetros que se seguirán durante la impresión. En la parte superior se despliegan cuadros en donde uno puede modificar el material, la densidad de relleno, el diámetro de la boquilla del extrusor y también podemos activar la opción “Supported”, esta última debe de estar activa en cada pieza o de lo contrario no se van a poder imprimir.

Figura 39.Espacio de trabajo UltiMaker Cura
En este caso se utilizó una densidad del 30% y una boquilla de 0.4[mm] de diámetro, como se mencionó anteriormente, se utilizaron dos máquinas con diferente material, por lo que este parámetro va a variar dependiendo de cada pieza. Una vez que se tienen los modelos con la postura necesaria y todos los parámetros configurados, se selecciona la opción “Slice” para que el programa genere el laminado capa por capa de la pieza, dado que se tiene

Open – Puma UNAM | 35/40
AUTÓNOMA DE MÉXICO | F A C U L T A D D E I N G E N I E R Í A DIVISIÓN DE INGENIERÍA MECÁNICA E INDUSTRIAL Robótica – Proyecto

un Shell que únicamente considera la superficie exterior del cuerpo, se rellena el interior tomando interpolaciones de diversos puntos que describen la geometría de la pieza, siguiendo un mallado que rellena el Shell.

Figura 40. Preview de las piezas
Una vez que termina el proceso de Slice, el programa dos deja ver una vista previa de los componentes que se van a imprimir, indicando un tiempo aproximado de impresión y una cantidad de material a utilizar. El Slice también se encarga de generar los soportes que se necesiten para que pueda llevarse a cabo la manufactura.
Una vez que terminamos UltiMaker Cura genera un archivo con extensión “.gcode” que podemos guardar en una memoria micro SD, este archivo ya puede ser leído por nuestra máquina y será el que le ingresemos por medio de la unidad de memoria portátil para poder avanzar al siguiente paso en la fabricación.
Antes de dar inicio a la manufactura fue necesario aprender algunos parámetros de configuración para que la impresora pudiera cumplir con su tarea, es de suma importancia este paso ya que de lo contrario ninguna pieza va a poder ser fabricada. Cada impresora se ajustó de manera distinta sin embargo para ambas se utilizaron los mismos parámetros.
Para la calibración de la primera máquina con filamento de PLA fue necesario nivelar la cama caliente, se ubicó el extrusor en el “Home” y después se utilizó una hoja blanca de papel para medir la distancia en el extrusor y la cama, la cual debe de ser de aproximadamente 0.4[mm] (La medida del grosor de la hoja). Se ajustó la distancia por medio de los tornillos


Open – Puma UNAM | 36/40
AUTÓNOMA DE MÉXICO | F A C U L T A D D E I N G E N I E R Í A DIVISIÓN DE INGENIERÍA MECÁNICA E INDUSTRIAL Robótica – Proyecto

puestos en la base para lograr la nivelación correcta al poner la hoja entre la cama y la boquilla del extrusor y se apretaban o aflojaban los tornillos hasta que se presionara la hoja sin sujetarla completamente, esta operación se llevó a cabo dos veces en diferentes puntos de la cama.
Para la máquina con filamento de PETG, dado que esta cuenta con un sensor para detectar la distancia, no fue necesario hacer la prueba con la hoja de papel, al igual que en el caso anterior se llevó el extrusor a la posición de “Home” y simplemente se niveló la cama caliente utilizando un calibrador vernier, midiendo que fuera la misma distancia de la cabeza de los cuatro tornillos a la cama. Después se utilizó la función de autonivelación que tiene la impresora en donde, de manera automática, se lleva la boquilla del extrusor a distintos puntos de la cama y por medio del sensor se ajusta la distancia entre ambas partes.
Una vez calibradas las impresoras podemos comenzar nuestro proceso de manufactura, la interfaz de ambas es idéntica lo que facilita el manejo. Dentro del menú se debe de seleccionar la opción Print, posteriormente se selecciona el archivo con las piezas que se desean imprimir y listo.
La temperatura que se seleccionó para la cama caliente fue de 60°C, la del extrusor varió un poco dependiendo del material pero se manejaron temperaturas de 210°C para el PLA y 215° para el PETG. Antes de que comience la impresión también fue necesario rociar la cama caliente con un fijador en aerosol, esto con la intención de que las piezas no se despeguen durante el proceso y nuestra impresión falle.

Figura 41.Proceso de impresión con PLA


Open – Puma UNAM | 37/40
AUTÓNOMA DE MÉXICO | F A C U L T A D D E I N G E N I E R Í A DIVISIÓN DE INGENIERÍA MECÁNICA E INDUSTRIAL Robótica – Proyecto

Durante la etapa de diseño de las piezas se realizaron distintas iteraciones debido a la falta de experiencia con este proceso de manufactura y la falta de la prueba de colisiones en el ensamble durante las primeras 3 versiones de la lista de componentes. A continuación se muestran algunos de los modelos resultantes de estas iteraciones, en donde algunas de estas piezas pudieron cumplir con las dimensiones y requerimientos para el ensamble físico.

Figura 42.Prototipos de las piezas a ensamblar
Después de que todas las piezas fueran fabricadas se procedió al ensamble del brazo robótico. Como se mencionó al incido, el brazo robótico al contar con 5 grados de libertad, necesitará el mismo número de actuadores que nos permitan realizar los diferentes movimientos, por lo que se utilizaron de 5 servomotores AX-18A. Además de los servos es necesaria una pinza que pueda abrir y cerrar con el objetivo de poder manipular objetos.
Para poder ensamblar se utilizaron tornillos M3 con sus respectivas tuercas, los actuadores cuentan con barrenos y guías para poder atornillar las piezas, hay que tener mucho cuidado de utilizar estos espacios designados para el ensamble y no dañar el motor. Fue necesaria la utilización de un desarmador con punta de cruz y una llave Allen para poder llevar a cabo el ensamble ya que la cabeza de algunos tornillos era diferente.


Open – Puma UNAM | 38/40
AUTÓNOMA DE MÉXICO | F A C U L T A D D E I N G E N I E R Í A DIVISIÓN DE INGENIERÍA MECÁNICA E INDUSTRIAL Robótica – Proyecto

Figura 43. Proceso de ensamble
Primero se procedió a ensamblar las piezas a las guías laterales e inferiores de los servos antes de atornillar en los ejes, esto con el objetivo de facilitar la visualización del orden de los eslabones con base al modelo hecho en el CAD Fusion. Posteriormente se conectaron los servos en serie siguiendo el orden correcto teniendo cuidado de conectar los cables en el puerto correcto, cada servo tiene un puerto de entrada que se debe conectar con el actuador anterior y otro de salida en donde se deberá conectar con el actuador siguiente.

Figura 44.Ensamble del brazo vista lateral
Como al momento de realizar el ensamble aún no se contaba con la base del robot, sólo se pudieron ensamblar 4 servomotores, ya que el faltante es el que se ensamblaba con la base faltante, sin embargo, con el modelo realizado se pudieron realizar las pruebas de funcionamiento.

Open – Puma UNAM | 39/40
AUTÓNOMA DE MÉXICO | F A C U L T A D D E I N G E N I E R Í A DIVISIÓN DE INGENIERÍA MECÁNICA E INDUSTRIAL Robótica – Proyecto

## CONCLUSIÓN

Con base a lo desarrollado en este proyecto podemos afirmar que cuando se trabaja en un proyecto grande cada parte es importante, y es indispensable verificar hasta los detalles más pequeños. Tal es el caso de las medidas y características de los diseños, ya que si estas están mal la impresión en 3D no será la mejor, causando contratiempos o incluso errores que solo pueden ser corregidos volviendo a diseñar e imprimir, generando una gran pérdida de tiempo y material. A su vez aprendimos que en ocasiones el problema puede ser ocasionado por la plataforma que empleamos, tal fue nuestro caso con MATLAB que presentaba problemas para comunicarse con los servomotores.
Pese a la falta de tiempo con la que trabajamos logramos hacer una revisión y corrección de las piezas para poder manufacturarlas mediante el uso de una impresora 3D, comprendimos e implementamos la interfaz de los motores y logramos obtener un avance considerable a pesar de las adversidades que se nos presentaron en este semestre. Por lo que podemos concluir que se alcanzaron la mayoría de los objetivos planteados al comienzo del proyecto.
Se pudieron cumplir con tres de los cuatro objetivos planteados al inicio del proyecto, el objetivo particular de “Trabajar en una interfaz de control de los motores en Matlab para que el robot realice una tarea específica.” no se pudo Completar al 100% debido a los recursos computacionales con los que contaba la brigada y el software de Matlab presentó diversos problemas. Sin embargo, con el trabajo realizado por el equipo se logró cumplir con la premisa de que como futuros profesionistas en el campo de la ingeniería, pudimos aplicar los conocimientos aprendidos a lo largo del curso en una implementación práctica.

## COMENTARIOS

Nos gustaría sugerir que se preste una mayor atención a los diseños, ya que en la computadora puede parecer que están bien, pero al momento de imprimirlos en 3D y hacerle pruebas, tienden a fallar por errores mínimos.

Open – Puma UNAM | 40/40
AUTÓNOMA DE MÉXICO | F A C U L T A D D E I N G E N I E R Í A DIVISIÓN DE INGENIERÍA MECÁNICA E INDUSTRIAL Robótica – Proyecto

También nos gustaría sugerir que se trabaje con otra plataforma como Arduino o ROS para el desarrollo de la interfaz ya que MATLAB genera bastantes contratiempos.

## REFERENCIAS

[1] R. e-manual, «Open Manipulador-X,» 2017. [En línea]. Available: https://emanual.robotis.com/docs/en/platform/openmanipulator_x/overview/. [Último acceso: 04 junio 2024].
[2] S. SanDoRobotics, «SNAPPER ROBOT ARM,» 2024. [En línea]. Available: https://sandorobotics.com.mx/producto/rg-snapper/. [Último acceso: 04 junio 2024].
[3] G. Robots, «Base robot,» 2024. [En línea]. Available: https://www.generationrobots.com/en/401792-widowx-robot-arm-withouthttps://www.generationrobots.com/en/401792-widowx-robot-arm-without-servomotors.htmlservomotors.ht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 . [Último acceso: 04 junio 2024].
[4] Pascual, «Revisión para base de robot open-puma,» 2024. [En línea]. Available: https://github.com/arrg-mx/Open-UNAM/blob/main/Carpeta_2024_2/Base_robot/analisis%20de%20base%20robotica.pdf. [Último acceso: 04 junio 2024].
[5] GRABCAD, «Grabcad Community,» 2024. [En línea]. Available: https://grabcad.com/library/interbotix-phantomx-reactor-robot-arm-kit-1 . [Último acceso: 04 junio 2024].
[6] R. e. -. Manual, «AX-18F, AX-18A,» 2024. [En línea]. Available: https://emanual.robotis.com/docs/en/dxl/ax/ax-18a/. [Último acceso: 04 junio 2024].
[7] Gibran, «Pruebas de manufactura aditiva,» 2024. [En línea]. Available: https://github.com/arrg-mx/Open-UNAM/blob/main/Carpeta_2024_2/Pruebas%20de%20manufactura%20aditiva.pdf. [Último acceso: 04 junio 2024].

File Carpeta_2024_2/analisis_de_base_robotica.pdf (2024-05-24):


## Universidad Nacional Autónoma de México

## Facultad de Ingeniería

## División de Ingeniería Mecánica e IndustrialSemestre 2024-1

## Materia: Robótica (2135)

# “Revisión para base de robot open-puma”

## Semestre: 2024-1

## Fecha de entrega: 13 /Mayo/2024

## Profesor: M.I Erick Peña Medina

## Alumno: Pascual Hernández Daniel Alfonso

Se realizo la valoración para saber cómo se obtendría la base necesaria para continuar con el análisis del proyecto, para lo mismo se plantearon 3 opciones: Comprar la base, rediseñar la base, obtener un modelo CAD libre de un tercero.
Tras el análisis de las 3 opciones los resultados fueron los siguientes:
- Comprar a base:
En la tienda https://sandorobotics.com.mx/producto/rg-snapper/ (SandoRobotics) me informaron que este modelo en específico esta descontinuado por lo que no se puede

comprar con ellos.


Una segunda pagina española me dio un modelo parecido , con el precio indicado en la imagen


https://www.generationrobots.com/en/401792-widowx-robot-arm-withoutservomotors.html (https://www.generationrobots.com/en/401792-widowx-robot-arm-without-servomotors.html)

- Rediseñar la base: Teniendo el modelo físico que se encuentra en el laboratorio con ayuda de un vernier se podrían sacar medidas aproximadas, para lograr obtener un modelo en CAD para mandar a imprimirlo en 3D para realizar pruebas rápidas, corregir si es necesario alguna medida o realizarlo de algún otro material cuando se tenga certeza de su buen funcionamiento.
- Modelo CAD:
a) Logre encontrar un modelo semejante (totalmente modelado) tiene un precio total de 89$ MNX y movimiento desde la base es:


Brazo robótico de JJMAKER3D | Open manipulador
https://cults3d.com/es/modelo-3d/juegos/brazo-robotico
b) En GradCad logre encontrar el perfil donde un usuario modelo un robot semejante al que se tiene en el laboratorio https://grabcad.com/library/robotics-arm-10


El segundo modelado que encontré es del InterbotiX ViudaXL directamente del perfil
del | fabricante | aunque | se | desconoce | si | es | el | perfil | real | o | un | fake
(https://grabcad.com/trossen.robotics-1/models ) (https://grabcad.com/library/interbotix-widowxl-1


El tercer modelo de Kit de brazo robótico del reactor InterbotiX PhantomX (solo un archivo)

(https://grabcad.com/library/interbotix-phantomx-reactor-robot-arm-kit-1 )


Conclusión
El cad que se eligió fue el InterbotiX PhantomX por la facilidad de poder imprimirla en 3D en el laboratorio, dando seguimiento de análisis se dio pauta a realizar la base (por placas) a través de la cortadora laser que existe en el tercer piso del CIA.

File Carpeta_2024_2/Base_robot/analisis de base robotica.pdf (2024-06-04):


## Universidad Nacional Autónoma de México

## Facultad de Ingeniería

## División de Ingeniería Mecánica e IndustrialSemestre 2024-1

## Materia: Robótica (2135)

# “Revisión para base de robot open-puma”

## Semestre: 2024-1

## Fecha de entrega: 13 /Mayo/2024

## Profesor: M.I Erick Peña Medina

## Alumno: Pascual Hernández Daniel Alfonso

Se realizo la valoración para saber cómo se obtendría la base necesaria para continuar con el análisis del proyecto, para lo mismo se plantearon 3 opciones: Comprar la base, rediseñar la base, obtener un modelo CAD libre de un tercero.
Tras el análisis de las 3 opciones los resultados fueron los siguientes:
- Comprar a base:
En la tienda https://sandorobotics.com.mx/producto/rg-snapper/ (SandoRobotics) me informaron que este modelo en específico esta descontinuado por lo que no se puede

comprar con ellos.


Una segunda pagina española me dio un modelo parecido , con el precio indicado en la imagen


https://www.generationrobots.com/en/401792-widowx-robot-arm-withoutservomotors.html (https://www.generationrobots.com/en/401792-widowx-robot-arm-without-servomotors.html)

- Rediseñar la base: Teniendo el modelo físico que se encuentra en el laboratorio con ayuda de un vernier se podrían sacar medidas aproximadas, para lograr obtener un modelo en CAD para mandar a imprimirlo en 3D para realizar pruebas rápidas, corregir si es necesario alguna medida o realizarlo de algún otro material cuando se tenga certeza de su buen funcionamiento.
- Modelo CAD:
a) Logre encontrar un modelo semejante (totalmente modelado) tiene un precio total de 89$ MNX y movimiento desde la base es:


Brazo robótico de JJMAKER3D | Open manipulador
https://cults3d.com/es/modelo-3d/juegos/brazo-robotico
b) En GradCad logre encontrar el perfil donde un usuario modelo un robot semejante al que se tiene en el laboratorio https://grabcad.com/library/robotics-arm-10


El segundo modelado que encontré es del InterbotiX ViudaXL directamente del perfil
del | fabricante | aunque | se | desconoce | si | es | el | perfil | real | o | un | fake
(https://grabcad.com/trossen.robotics-1/models ) (https://grabcad.com/library/interbotix-widowxl-1


El tercer modelo de Kit de brazo robótico del reactor InterbotiX PhantomX (solo un archivo)

(https://grabcad.com/library/interbotix-phantomx-reactor-robot-arm-kit-1 )


Conclusión
El cad que se eligió fue el InterbotiX PhantomX por la facilidad de poder imprimirla en 3D en el laboratorio, dando seguimiento de análisis se dio pauta a realizar la base (por placas) a través de la cortadora laser que existe en el tercer piso del CIA.

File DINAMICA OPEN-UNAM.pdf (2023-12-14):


## FACULTAD DE INGENIERIA


DINÁMICA DEL ROBOT DE CINCO GRADOS DE LIBERTAD.

## Laureano Uribe Diego

## Pazarán García Jared

## Profesor: Erik Peña Medina

## Robótica

Semestre 2024-1

Objetivos:

Determinar la dinámica en cada uno de los eslabones usando el método de Newton-Euler.

Explicar de manera detallada el desarrollo de la dinámica.

Introducción:

El robot a continuación mostrado será el analizado el cual forma parte de la compañía OpenManipulator-X el cual es compatible con ROS el cual es una plataforma de código abierto compatible con OpenCR.


OpenManipulator (s.f) CAD del robot de 5 grados de libertad

El fin en cuestión del desarrollo de la dinámica, es sentar las primeras bases para próximas manipulaciones, por lo que la dinámica llega hasta la modelación de cada eslabón, y que con el desarrollo los siguientes integrantes del proyecto puedan entender cómo se llegó al modelo y por tanto puedan trabajarlo a las condiciones que se deseen. Recalcando que todo lo que se verá, está completamente basado en la notación y la clase de Robotica del profesor Erik Peña Medina del semestre 2024-1.

Desarrollo:

La dinámica de Newton-Euler en el plano es la utilizada, y como en cualquier análisis dinámico necesitamos un sistema de referencia desde el cual analizamos las fuerzas, como mencionamos se hace el análisis a partir de un eslabón, y el primero con el que se decide empezar es el de la pinza ya que este resulta ser más sencillo, después pasaremos con los eslabones intermedios.

Primero partimos de hacer un Diagrama de Cuerpo Libre (DCL), en el cual se establece el sistema de referencia Inercial {o}, y los sistemas de referencia que están pegados al eslabón y en el centro de masa del eslabón (este se hizo de manera general), {i}, {j}, {l}, respectivamente.


Las fuerzas ahora son colocadas

Donde:


Fex es una fuerza externa que podría actuar sobre el robot o el eslabón

Fac es la fuerza de aceleración debido a la masa del cuerpo cuando se acelera

W es el peso del cuerpo

Con base en la primera parte se pueden establecer las ecuaciones de balance de momentum lineal. Sin embargo y recordando que las fuerzas se encuentran en diferentes sistemas de referencia se tienen que proyectar en la base que requerimos en nuestro caso la base {i}.

∑Ftotales = Fex
i
j

+ Fac

i
l

+ R

i
o

oWl

Donde Fex

i
j

es la fuerza externa proyectada en el sistema {i}

Fac

i
l

es la fuerza de aceleración proyectada en el sistema {i}

oWl es el peso del eslabón.

R

i
o es la matriz de rotación sobre el eje z y que nos ayudará también a proyectar el peso sobre {i}

Cada una de las fuerzas se representa de la siguiente manera ya en el sistema {i}.

Fex

i
j

= [

Fexxi

Fexyi

]

Fac

i
l

= [

Facxi

Facyi

]

R

i
o = [

cosα −sinα
sinα cosα

]

oWl = [

Wxi
Wyi

]

Ahora para el balance de Momentum angular ponemos los vectores de posición que van desde el sistema {i} hacia las diferentes fuerzas ya que este es el sistema que se toma de referencia para hacer los momentos


Y entonces la ecuación de balance de momentum angular queda como

∑Mtotales = P
i
j × miacl + P

i

### l × mi g

i + P

i
j × Fex
j | + Ici
i | ωi
̇

i

Donde P

i
j

es el vector de posición que va de {i} a {j}

P

i
l

es el vector de posición que va de {i} a {l}

Ici

i
es la matriz de inercia debida al teorema de ejes paralelos

ωi

̇

i
es la velocidad angular del eslabón

Los vectores y matrices son representados como

P

i
j = [

Pjx

Pjy

]

P

i
l = [

Plx
0

]

ωi

̇

i = [

0
0
| ωiz

]

Ici

i | = [
Ixx | Ixy | Ixz
Ixy | Iyy | Iyz
Ixz | Iyz | Izz

]

Todo lo anterior fue para el eslabón final, es decir la garra o pinza del robot. En el caso de los eslabones intermedios viene a ser las mismas ecuaciones agregando una fuerza de agarre entre los eslabones.


Con la ventaja estratégica de que al ser el sistema {i} donde se hace el análisis dejando la ecuación de momentum angular igual, ya que la fuerza de agarre pasa por el punto de referencia. Y agregando la fuerza de agarre en el momentum lineal, además de que la fuerza de agarre ya no es necesario proyectarla en {i} ya que se encuentra ahí.

∑Ftotales = Fex
i
j

+ Fac

i
l

+ R

i
o

oWl + Fag

i
i

∑Mtotales = P
i
j × miacl + P

i

### l × mi g

i + P

i
j × Fex
j | + Ici
i | ωi
̇

i

Donde:

Fag

i
i

es la fuerza de agarre entre eslabones

Cabe resaltar que en la fuerza externa se puede incluir si se requiere la fuerza de agarre con el siguiente eslabón.

Teniendo a la fuerza de agarre como:

Fag

i
i

= [

Fagx

Fagy

]

Por lo tanto con esto se tiene una representación inicial para los siguientes compañeros que decidan trabajar con la dinámica y tengan una imagen más clara de lo que se necesitará en el proyecto a las condiciones que se quiera considerar.

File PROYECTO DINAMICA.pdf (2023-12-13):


## FACULTAD DE INGENIERIA


DINÁMICA DEL ROBOT DE CINCO GRADOS DE LIBERTAD.

Pazarán García Jared

Profesor: Erik Peña Medina

Robótica

Semestre 2024-1

Objetivos:

Determinar la dinámica en cada uno de los eslabones usando el método de Newton-Euler.

Explicar de manera detallada el desarrollo de la dinámica.

Introducción:

El robot a continuación mostrado será el analizado el cual forma parte de la compañía OpenManipulator-X el cual es compatible con ROS el cual es una plataforma de código abierto compatible con OpenCR.


OpenManipulator (s.f) CAD del robot de 5 grados de libertad

El fin en cuestión del desarrollo de la dinámica, es sentar las primeras bases para próximas manipulaciones, por lo que la dinámica llega hasta la modelación de cada eslabón, y que con el desarrollo los siguientes integrantes del proyecto puedan entender cómo se llegó al modelo y por tanto puedan trabajarlo a las condiciones que se deseen. Recalcando que todo lo que se verá, está completamente basado en la notación y la clase de Robotica del profesor Erik Peña Medina del semestre 2024-1.

Desarrollo:

La dinámica de Newton-Euler en el plano es la utilizada, y como en cualquier análisis dinámico necesitamos un sistema de referencia desde el cual analizamos las fuerzas, como mencionamos se hace el análisis a partir de un eslabón, y el primero con el que se decide empezar es el de la pinza ya que este resulta ser más sencillo, después pasaremos con los eslabones intermedios.

Primero partimos de hacer un Diagrama de Cuerpo Libre (DCL), en el cual se establece el sistema de referencia Inercial {o}, y los sistemas de referencia que están pegados al eslabón y en el centro de masa del eslabón (este se hizo de manera general), {i}, {j}, {l}, respectivamente.


Las fuerzas ahora son colocadas

Donde:


Fex es una fuerza externa que podría actuar sobre el robot o el eslabón

Fac es la fuerza de aceleración debido a la masa del cuerpo cuando se acelera

W es el peso del cuerpo

Con base en la primera parte se pueden establecer las ecuaciones de balance de momentum lineal. Sin embargo y recordando que las fuerzas se encuentran en diferentes sistemas de referencia se tienen que proyectar en la base que requerimos en nuestro caso la base {i}.

∑Ftotales = Fex
i
j

+ Fac

i
l

+ R

i
o

oWl

Donde Fex

i
j

es la fuerza externa proyectada en el sistema {i}

Fac

i
l

es la fuerza de aceleración proyectada en el sistema {i}

oWl es el peso del eslabón.

R

i
o es la matriz de rotación sobre el eje z y que nos ayudará también a proyectar el peso sobre {i}

Cada una de las fuerzas se representa de la siguiente manera ya en el sistema {i}.

Fex

i
j

= [

Fexxi

Fexyi

]

Fac

i
l

= [

Facxi

Facyi

]

R

i
o = [

cosα −sinα
sinα cosα

]

oWl = [

Wxi
Wyi

]

Ahora para el balance de Momentum angular ponemos los vectores de posición que van desde el sistema {i} hacia las diferentes fuerzas ya que este es el sistema que se toma de referencia para hacer los momentos


Y entonces la ecuación de balance de momentum angular queda como

∑Mtotales = P
i
j × miacl + P

i

### l × mi g

i + P

i
j × Fex
j | + Ici
i | ωi
̇

i

Donde P

i
j

es el vector de posición que va de {i} a {j}

P

i
l

es el vector de posición que va de {i} a {l}

Ici

i
es la matriz de inercia debida al teorema de ejes paralelos

ωi

̇

i
es la velocidad angular del eslabón

Los vectores y matrices son representados como

P

i
j = [

Pjx

Pjy

]

P

i
l = [

Plx
0

]

ωi

̇

i = [

0
0
ωiz

]

Ici

i | = [
Ixx | Ixy | Ixz
Ixy | Iyy | Iyz
Ixz | Iyz | Izz

]

Todo lo anterior fue para el eslabón final, es decir la garra o pinza del robot. En el caso de los eslabones intermedios viene a ser las mismas ecuaciones agregando una fuerza de agarre entre los eslabones.


Con la ventaja estratégica de que al ser el sistema {i} donde se hace el análisis dejando la ecuación de momentum angular igual, ya que la fuerza de agarre pasa por el punto de referencia. Y agregando la fuerza de agarre en el momentum lineal, además de que la fuerza de agarre ya no es necesario proyectarla en {i} ya que se encuentra ahí.

∑Ftotales = Fex
i
j

+ Fac

i
l

+ R

i
o

oWl + Fag

i
i

∑Mtotales = P
i
j × miacl + P

i

### l × mi g

i + P

i
j × Fex
j | + Ici
i | ωi
̇

i

Donde:

Fag

i
i

es la fuerza de agarre entre eslabones

Cabe resaltar que en la fuerza externa se puede incluir si se requiere la fuerza de agarre con el siguiente eslabón.

Teniendo a la fuerza de agarre como:

Fag

i
i

= [

Fagx

Fagy

]

Por lo tanto con esto se tiene una representación inicial para los siguientes compañeros que decidan trabajar con la dinámica y tengan una imagen más clara de lo que se necesitará en el proyecto a las condiciones que se quiera considerar.

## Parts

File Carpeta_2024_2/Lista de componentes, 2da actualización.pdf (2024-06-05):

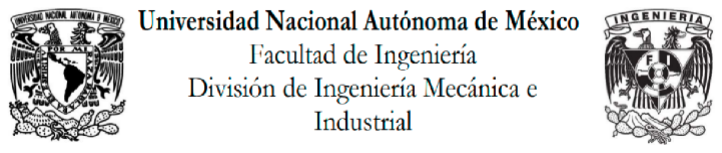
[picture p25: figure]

Robótica

Semestre 2024-2

Lista de componentes. (Segunda actualización)

Alumno: Javier Rivera Moreno

Parte | Imagen | Descripción | # de partes a imprimir

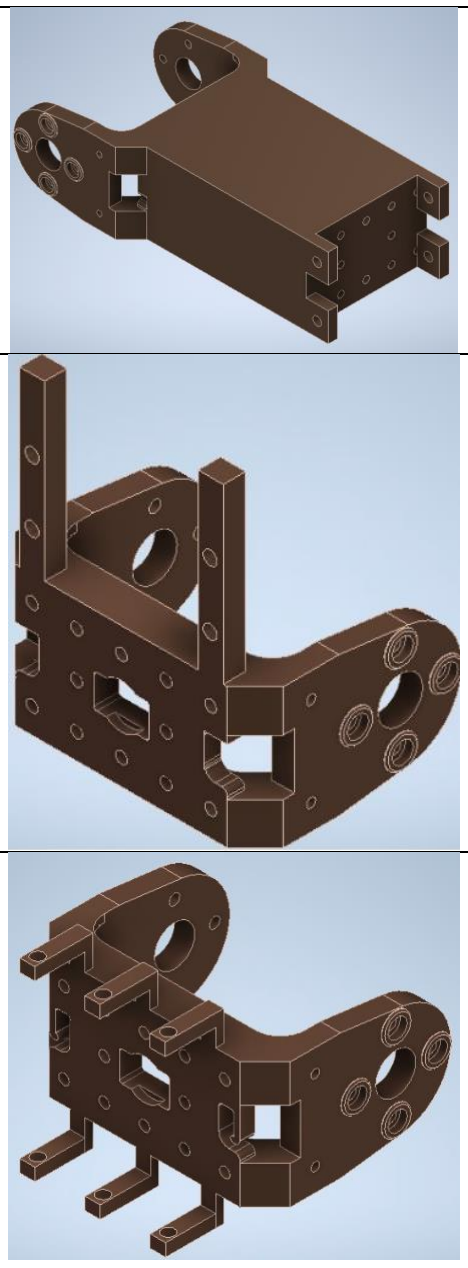
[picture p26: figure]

FP04-F2_1 | | Partes constitutivas del brazo | 2
FP04-F2_2 | | Unión del motor en control del gripper | 1
FP04-F2_3 | | Unión del motor de la base con el primer motor del brazo | 1

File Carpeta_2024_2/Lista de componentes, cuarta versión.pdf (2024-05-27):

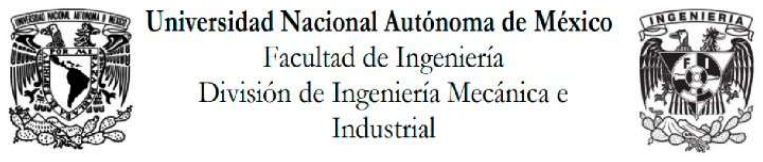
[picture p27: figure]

Robótica

Semestre 2024-2

Lista de componentes. (Cuarta versión)

Alumnos: Javier Rivera Moreno

Colima Flores Mauricio Gibran

Parte | Imagen | Descripción | # de partes a imprimir

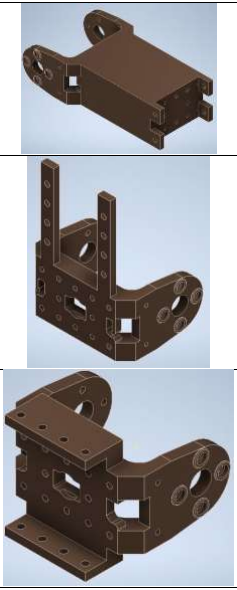
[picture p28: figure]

FP04_2V1 | | Partes constitutivas del brazo | 2
FP04_3V2 | | Unión del motor en control del gripper | 1
FP04_1V3 | | Unión del motor de la base con el primer motor del brazo | 1

Tabla 1. Lista de componentes

Ensamble

A la hora de realizar el ensamble se realizó la prueba para identificar si había colisiones que pudieran imposibilitar el ensamble, sin embargo, a la hora de correr la prueba en Inventor no se encontraron colisiones

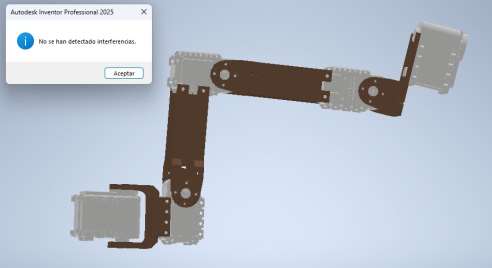
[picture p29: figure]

Imagen 1. Ensamble vista A con prueba de colisiones

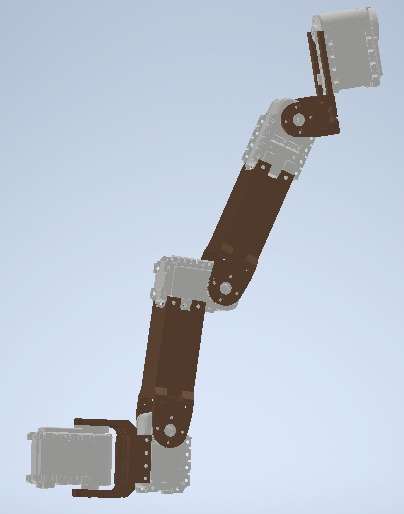
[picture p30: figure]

Imagen 1. Ensamble vista B con prueba de colisiones

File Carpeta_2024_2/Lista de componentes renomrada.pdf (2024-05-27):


Robótica

Semestre 2024-2

Lista de componentes. (Tercera actualización)

Alumno: Javier Rivera Moreno

Parte | Imagen | Descripción | # de partes a imprimir

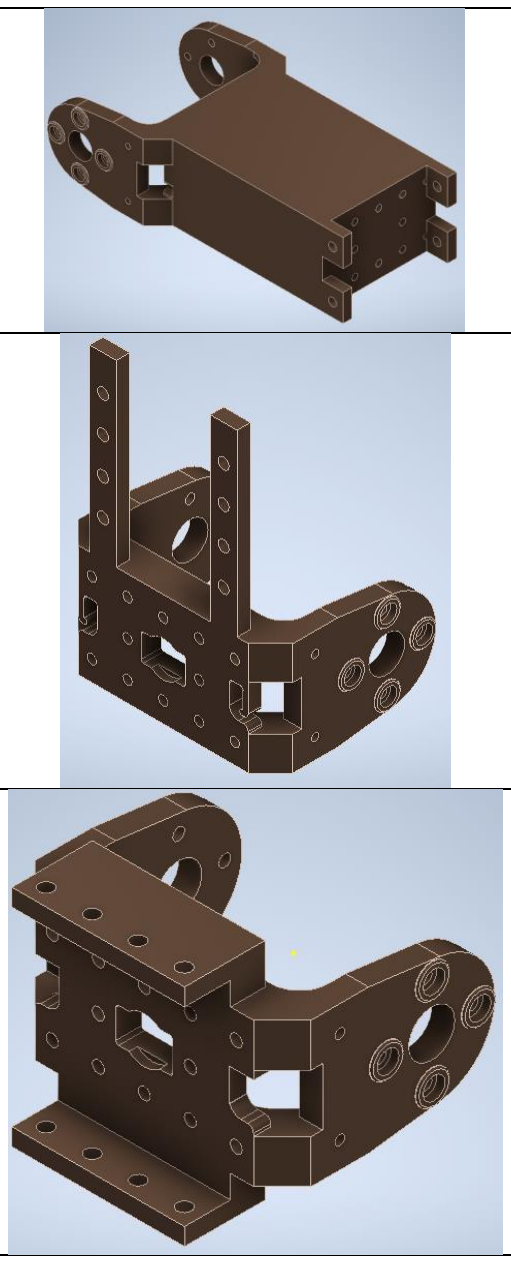
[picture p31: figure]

FP04-F2_1 | | Partes constitutivas del brazo | 2
FP04-F2_2 | | Unión del motor en control del gripper | 1
FP04-F2_3 | | Unión del motor de la base con el primer motor del brazo | 1

Ensamble

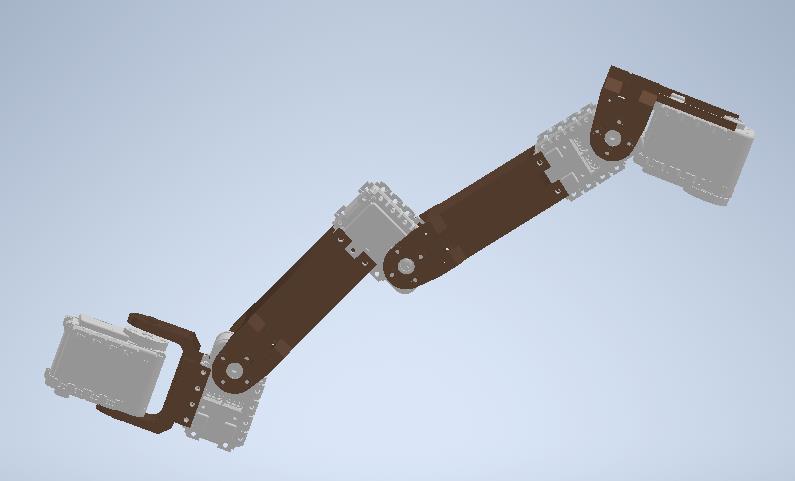
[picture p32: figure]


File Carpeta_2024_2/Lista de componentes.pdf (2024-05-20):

Robótica

Semestre 2024-2

Lista de componentes

Alumno: Javier Rivera Moreno

LISTA DE COMPONENTES

Parte | Imagen | Descripción | # de partes a imprimir

Parte de la articulación; Parte de la base; Parte del brazo; Parte del antebrazo

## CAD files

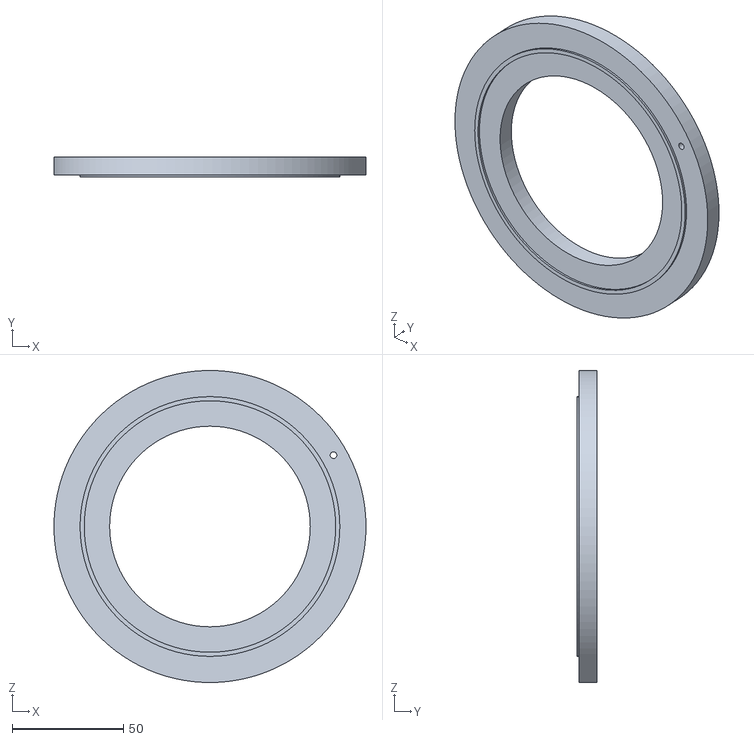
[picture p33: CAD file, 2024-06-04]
Carpeta_2024_2/Base_robot/piezas_y_planos/piezas_separado/3d_1.stl
140.0 x 9.00 x 140.0

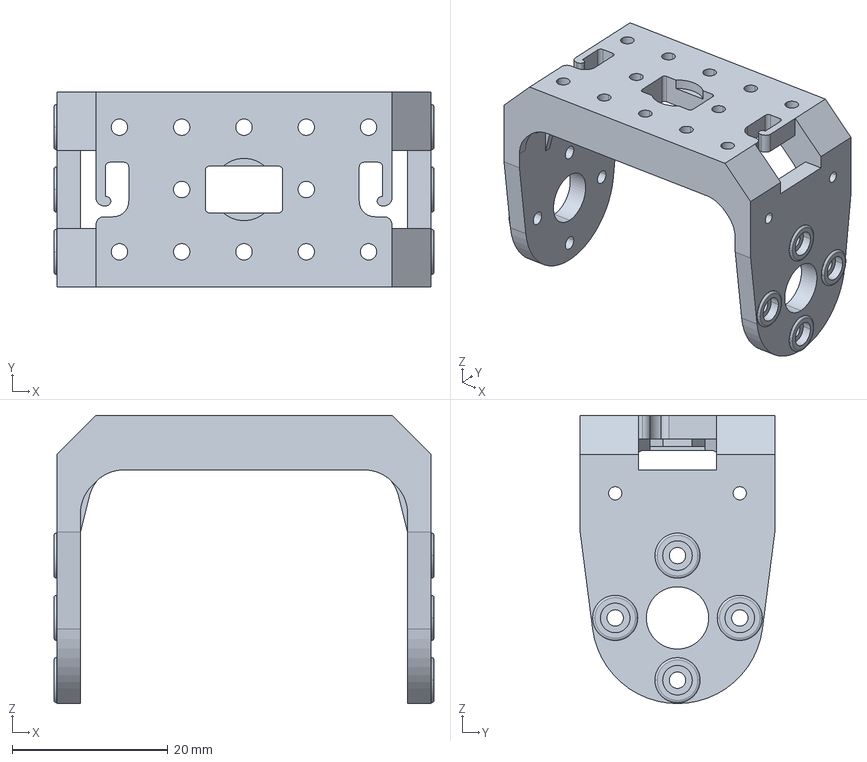
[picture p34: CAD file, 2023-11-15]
FP04-F2.stp
48.8 x 25.0 x 37.0 mm

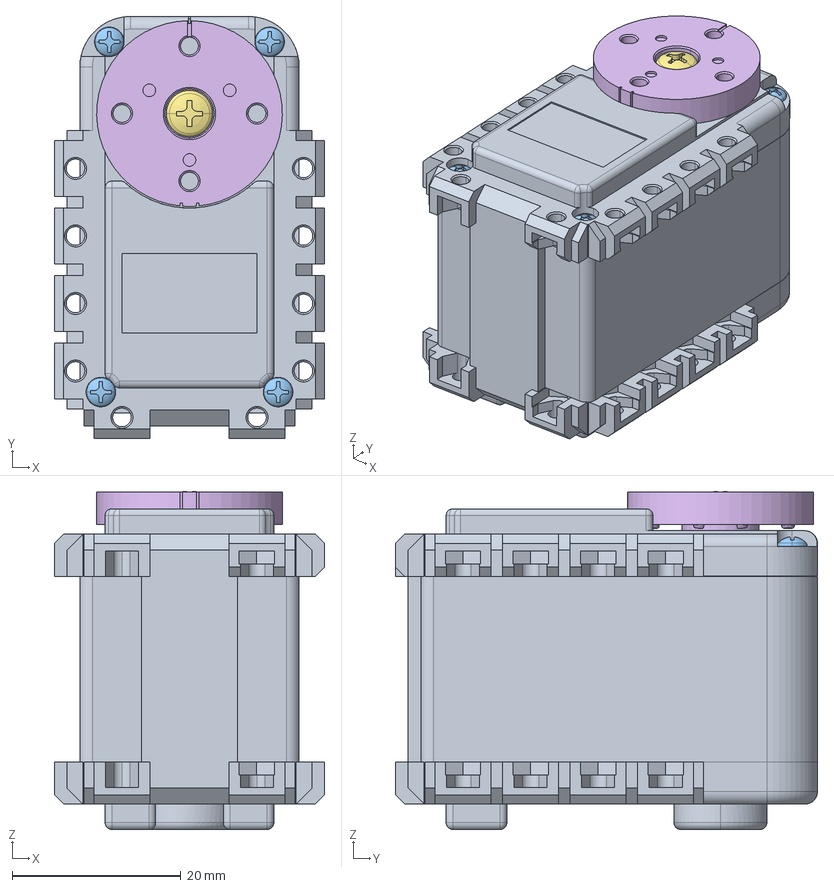
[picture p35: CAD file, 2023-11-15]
AX-12A.stp
32.0 x 50.0 x 40.0 mm
PRT0001
PRT0002
PRT0003 x 4
PRT0004 x 2
PRT0005
PRT0006
PRT0007

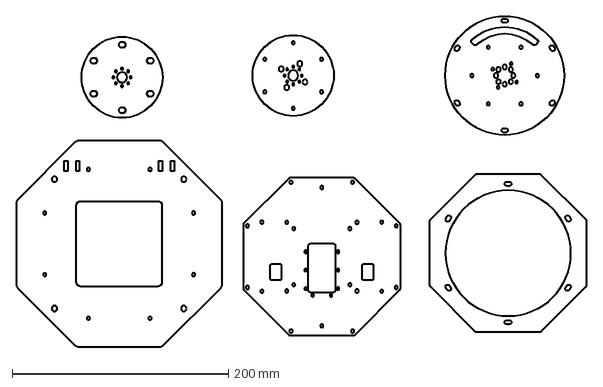
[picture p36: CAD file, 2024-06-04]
Carpeta_2024_2/Base_robot/piezas_y_planos/piezas_separado/base_comlpeta_cortar_.dxf
528.0 x 306.0 mm

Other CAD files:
Carpeta_2024_2/Base_robot/piezas_y_planos/piezas_separado/paracortar_exportado.dwg
Carpeta_2024_2/Base_robot/piezas_y_planos/piezas_separado/paracortar.dwg
Carpeta_2024_2/Base_robot/piezas_y_planos/base_con_separadores.iam
Carpeta_2024_2/Base_robot/piezas_y_planos/piezas_separado/3d_1.ipt
Carpeta_2024_2/Base_robot/piezas_y_planos/piezas_separado/OldVersions/3d_1.0001.ipt
Carpeta_2024_2/Base_robot/piezas_y_planos/piezas_separado/base_enmedio.ipt
Carpeta_2024_2/Base_robot/piezas_y_planos/piezas_separado/base_inferior.ipt
Carpeta_2024_2/Base_robot/piezas_y_planos/piezas_separado/base_sup.ipt
Carpeta_2024_2/Base_robot/piezas_y_planos/piezas_separado/base_sup_mov.ipt
Carpeta_2024_2/Base_robot/piezas_y_planos/piezas_separado/base_sup_mov_2.ipt
Carpeta_2024_2/Base_robot/piezas_y_planos/piezas_separado/bases_juntas.ipt
Carpeta_2024_2/Base_robot/piezas_y_planos/piezas_separado/tapa_base_sup.ipt
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

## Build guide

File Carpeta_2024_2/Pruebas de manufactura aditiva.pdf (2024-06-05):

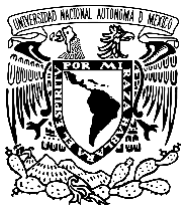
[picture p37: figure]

# Universidad nacional autónoma de México

# Facultad ingeniería

# División de ingeniería mecánica e industrial

# Semestre: 2024-2

# Materia: Robótica

# “Pruebas de manufactura aditiva”

# Profesor: M.I Erick Peña Medina

# Alumnos: Colima Flores Mauricio Gibran

# Pascual Hernández Daniel Alfonso

Al inicio del proyecto se contaba con una lista previa de las piezas que se proponían para el ensamblado del robot, se tenía también una primera propuesta de ensamble por lo que la primera tarea a realizar comprendía de manufacturar dichas piezas por medio de impresión 3D. La impresora a utilizar fue una Ender-3 V2 de la marca CREALITY, con un filamento de PLA. La lista previa de piezas se muestra en la tabla 1.

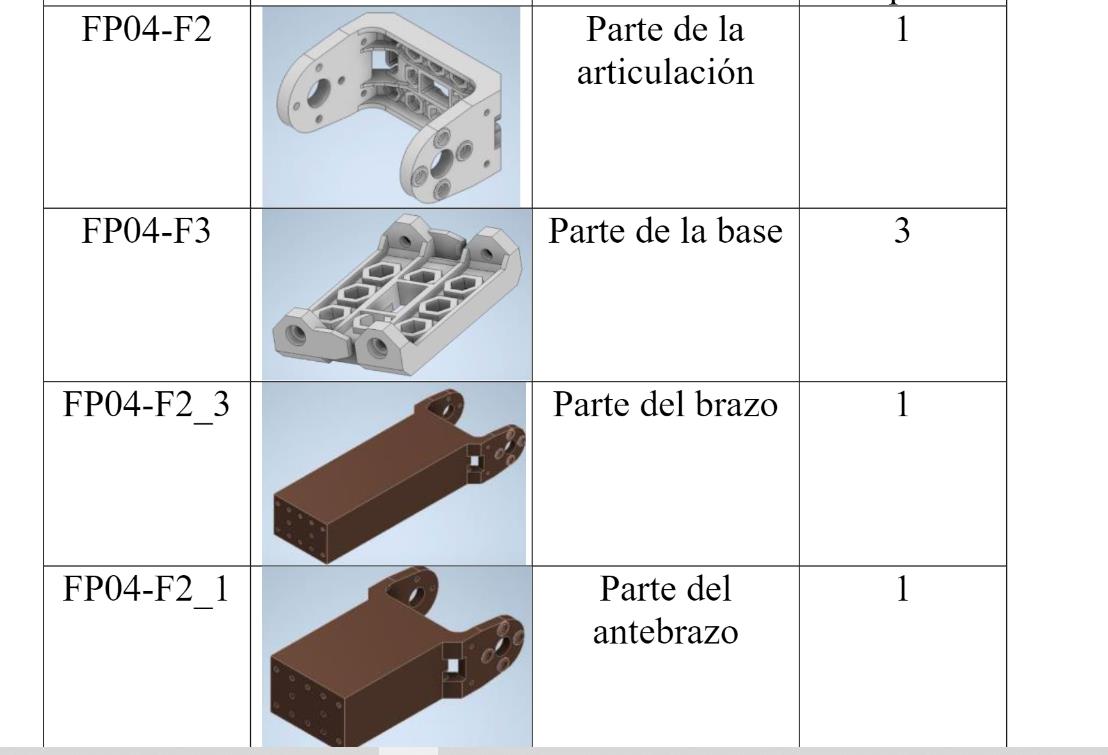
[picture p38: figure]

Tabla 1. Versión 1 lista de componentes a manufacturar

A la hora del realizar el análisis las piezas, el equipo se percató de la falta de método de ensamble (solo estaban fijas, en el software inventor) por lo que se tuvo que realizar una etapa de rediseño anterior a la manufactura en diversas piezas para lograr ensamblados físicos.

Por cuestiones de tiempo se tomó la decisión de sustituir la pieza “FP04_F2_3” con una segunda pieza “FP04_F2_3”. Por otro lado, se decidió prescindir de la pieza “FP04_F3” y simplemente realizar modificaciones a la pieza “FP04_F2” y elaborar dos piezas nuevas que puedan cumplir con la función del ensamble.

Para la primera iteración, dado que ningún integrante de la brigada tenía conocimientos previos de impresión en 3D, se decidió comenzar con una de las modificaciones a partir de la pieza “FP04_F2” y el rediseño de “FP04_F2_1”, las cuales serán renombradas como “FP04_1V1” y “FP04_2V1” respectivamente, sin embargo, hubo diversas fallas en la manufactura. A continuación, presentamos las piezas que se imprimieron junto con la falla que presentaron.

- FP04_2V1: El rediseño de “FP04_F2_1” consistió en la adición de muescas barrenadas que permitieran ensamblar por medio de tornillos. La falla que presentó a la hora de su impresión se debió a que en un punto de la impresión se dejó de extruir. Dos propuestas de solución dada fue vigilar la impresora de manera continua, dando unas vueltas extras al carrete del filamento cada 2 min para que no dejara de extruir y subir la temperatura del extrusor, de 200°C a 210°C.

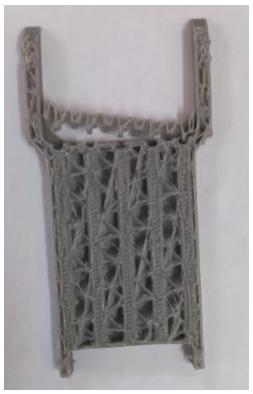
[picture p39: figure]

Imagen 1. Prueba 1 impresión FP04_2V1

Se realizó una segunda prueba bajo las sugerencias para solucionar el problema y no se tuvieron más fallas para esta pieza. Se realizó también una segunda impresión de esta pieza para sustituir a “FP04_F2_3”

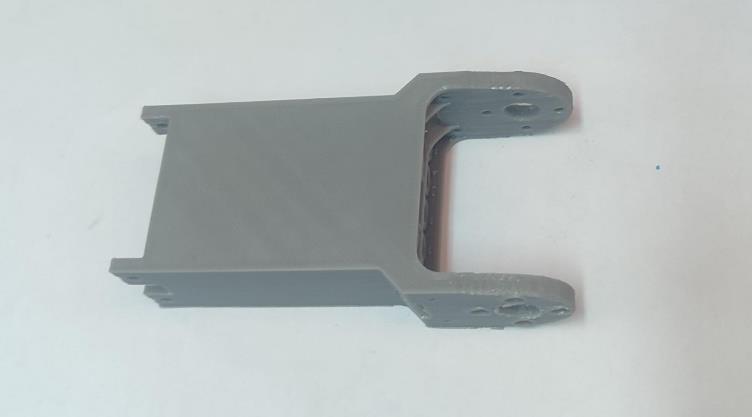
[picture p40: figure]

Imagen 2. Prueba 2 impresión FP04_2V1

- FP04_1V1: Se modifico la pieza “FP04_F2” agregándole columnas con barrenos para una por tornillos. La prueba 1 presentó la misma falla por parte de la impresora y se tuvo que recurrir a una prueba 2. Al final de la operación, las columnas eran demasiado delgadas, estas columnas presentaron fracturas, por lo que se tuvo que modificar una segunda vez para darle un mayor grosor, considerando el método de unión. Al rediseño de FP04_1V1 se le nombró “FP04_1V2”.

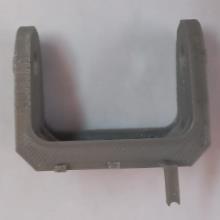
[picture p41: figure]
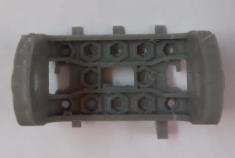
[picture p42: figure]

Imagen 3a. Prueba 2 impresión FP04_1V1 Imagen 3b. Prueba 2 impresión FP04_1V1

- FP04_3V1: Otra de las modificaciones que se le realizaron a “FP04_F2” fue para elaborar la pieza FP04_3V1, la cual presentaba otra configuración en sus columnas para ensamblar un servo en su posición correspondiente, dado las constantes fallas en la impresora 3D se utilizó una segunda impresora modelo Ender-3 V2 Neo con un filamento de PETG, ahora se podía trabajar con dos impresoras al mismo tiempo para agilizar los tiempos. No hubo problemas en la impresión sin embargo a la hora de probar el ensamble con el servomotor, la geometría diseñada no coincidía con las dimensiones del servo, por lo que se tuvo que rediseñar bajo el nombre de FP04_3V2.

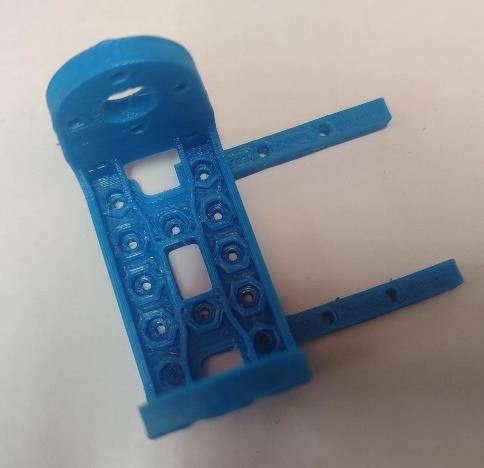
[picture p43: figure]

Imagen 4. Prueba impresión FP04_3V1

- FP04_1V2: Después de rediseñar nuevamente FP04_1V1 para hacer más robustas las columnas de sujeción se obtuvo la pieza FP04_1V2, se imprimió con la impresora de filamento PLA y no hubo problemas durante la manufactura, sin embargo se presentó también un problema en cuanto a las dimensiones de la pieza a la hora de ensamblarla, por lo que se tuvo que hacer un tercer diseño.

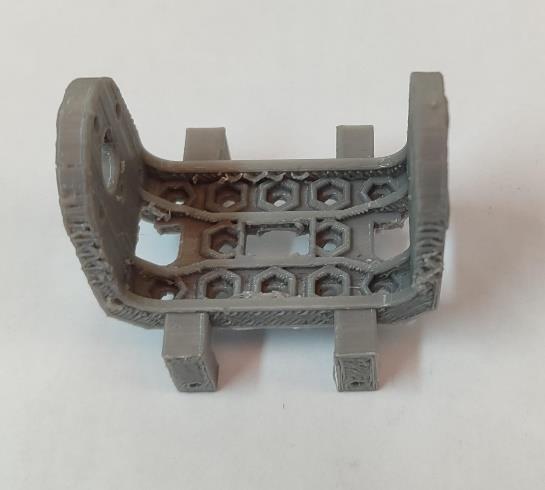
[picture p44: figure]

Imagen 5. Prueba impresión FP04_1V2

Para la base del robot igualmente se decidió imprimir una pieza la cual se denominó como 3d_1.ipt, solo re realizo un intento en esa pieza puesto que salió con las dimensiones adecuadas al primer intento.

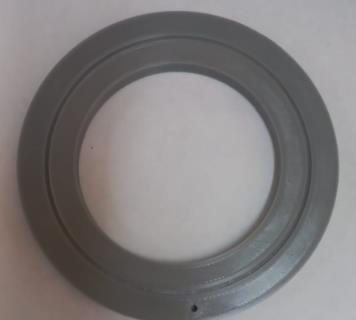
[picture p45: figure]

Imagen 6. Impresión 3d_1

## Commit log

2023-11-15 Add files via upload
    Cad motor
    [AX-12A.stp, FP04-F2.stp, FP04-F5.stp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]
2024-05-27 Add files via upload
    Esta lista toma en cuenta las iteraciones anteriores sobre las piezas del robot y el ensamble con la prueba de ensamble que contempla las colisiones, se realizó esta lista y ensamble antes de imprimi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
2024-06-05 Add files via upload
    En este documento viene una explicacion de las distintas iteraciones que se realizaron durante las pruebas en impresión 3D, contando las fallas en la máquina así como fallas en los diseños de las pie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
